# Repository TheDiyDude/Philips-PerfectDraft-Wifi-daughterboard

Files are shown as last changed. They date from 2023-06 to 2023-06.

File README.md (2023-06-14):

# Wifi Extension Board for Philips Perfect Draft (not Pro)
```
Ther are a couple of older approaches with potentiometers and switches to set a desired beer temperature.
Standard configuration is 3°C and sometimes this is to cold. Or you want to save energy. Which is not possible.
Here you can build your own PCB or other board type to add Wifi capabilities to your Perfect Draft machine (not Pro).

NOTE: Please pay additional attention if you work with high-voltage electricial power. If you are not aware of security when working with electricial power dont do this project. I am not responsible if you hurt youself or others. Your household AC current is between 110 and 240 volts and can kill you. Wiring errors lead into fire or turn your project into a leathal weapon!This is a diy project and you have to know what you are doing and think before you do something. Ok, I am a notorious german and we love these safety instructions. 
```

```
Features: 
  Wifi enabled
  Wifi Setup AP Mode (Wifi credentials stored in EEPROM)
  OTA Updates
  Set Cooling Temperature via Webbrowser http://PerfectDraft.local or IP
  Bypass your settings and use orginal NTC value (to see correct Temp after 5 Minutes)
  Use Fast Temp Buttons: 7°C, 10°, 11° C
  Save your setting within EEPROM and set after every reboot automatically
```
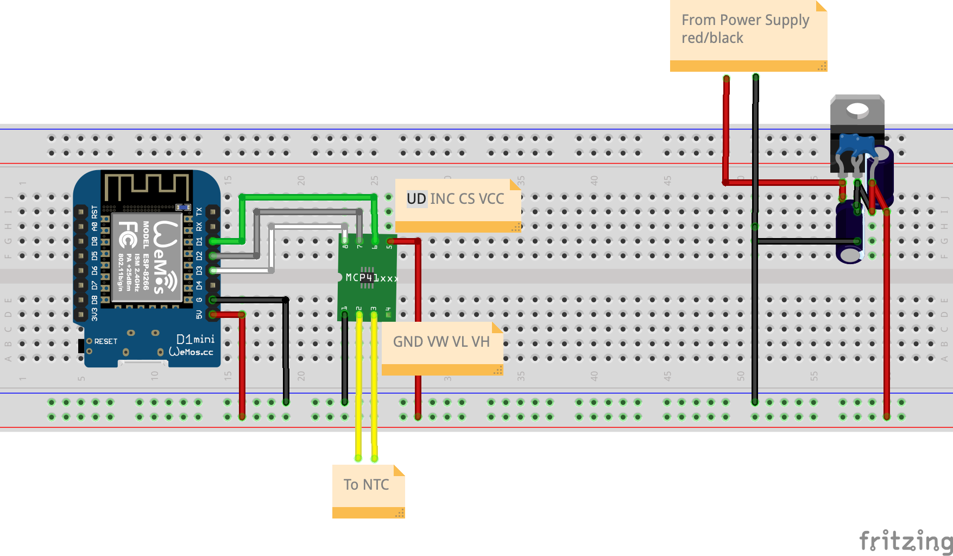
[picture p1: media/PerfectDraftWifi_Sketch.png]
Fritzing Sketch


```
Use a digital potentiometer like X9C103S (10kOhm) and connect the Pins:
VCC to 5V Pin 1
GND to 5V Pin 2
CS  to D1 Mini Pin D1
INC to D1 Mini Pin D2
U/D to D1 Mini Pin D3
VL  to one of the wires from the NTC connector (PD PCB)
VW  to the wire you have choose before (see description below)
```
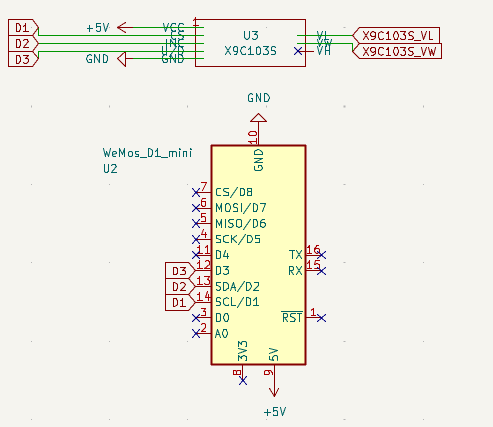
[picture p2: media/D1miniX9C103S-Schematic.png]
WemosD1-Wiring

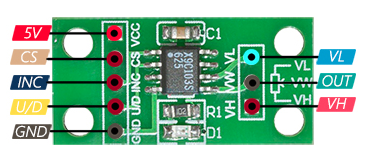
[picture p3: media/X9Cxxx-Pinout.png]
X9C103S


```
Remove the connector from PD PCB and add a Y connector. 
Choose one Pin from the PD PCB male connector labeled NTC and connect that wire to VL (X9C103S). 
The VW wire connect to the female connector (original) that was connected to the PD PCB before. 
The other Pin from the PCB labeled NTC connect directly to the female connector (original). 
```
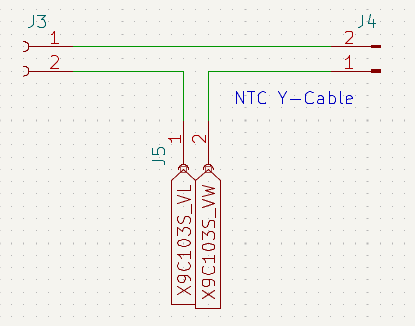
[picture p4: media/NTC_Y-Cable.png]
X9C103S_Y-Cable

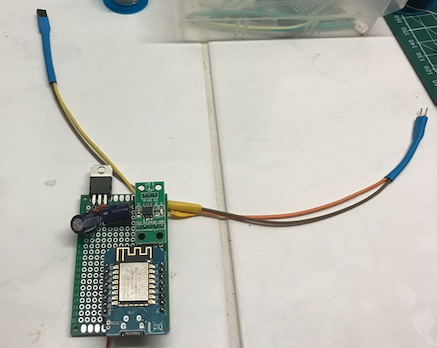
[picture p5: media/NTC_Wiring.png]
NTC Wiring


```
It is possible to use the machines power supply as it is already DC and 10.6V - 
apply this standard stabilized power converter to get 5V DC from 10.6 V DC:

Input  Pin 1 to PD red wire
Input  Pin 2 to PD black wire
Output Pin 1 to D1 Mini Pin 5V
Output Pin 2 to D1 Mini Pin get

See the second picture below to build a power supply Y-connector. Use the same cable connectors and connect red to PCB and to LM7805 Input Pin 1 - same to the black wire but connect that to Input Pin 2 (GND).
```
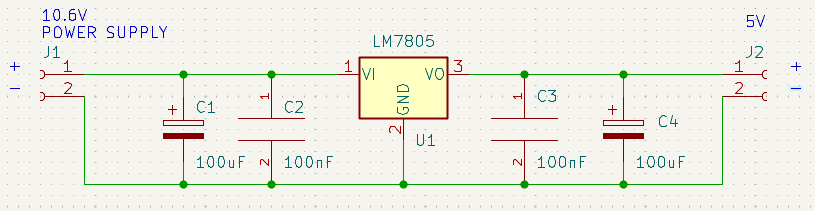
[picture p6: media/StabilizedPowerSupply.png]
stabilized power converter

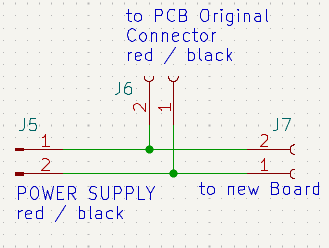
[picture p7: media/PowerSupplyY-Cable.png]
PowerSupplyY-Connector2

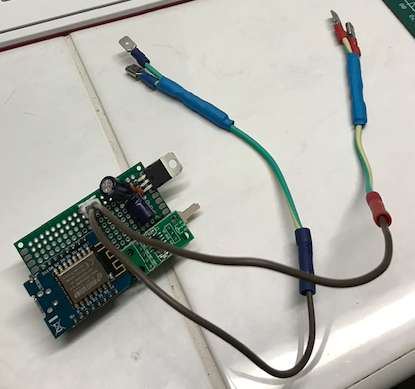
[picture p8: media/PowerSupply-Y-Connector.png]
PowerSupplyY-Connector

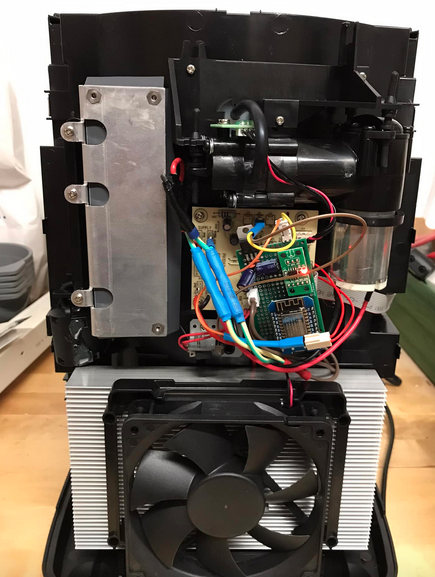
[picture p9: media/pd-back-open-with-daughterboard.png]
added-daughterboard

```
For communication with the X9C103S digital potentiometer I use the following supporting library:
   https://github.com/lucyamy/LapX9C10X.git
I do not know if this lib will change and I have put latest working copy to Libs folder. 
Add this ZIP library to your project.

Ensure to change your SSID and credentials before uploading the firmware. See firmware/Credentials.h
Ensure to change the default OTA credentials before uploading - default OTA upload password is 'pd2023'
Build the firmware and if you have done the wiring correctly you can see the Perfect Draft Wifi Website:
```
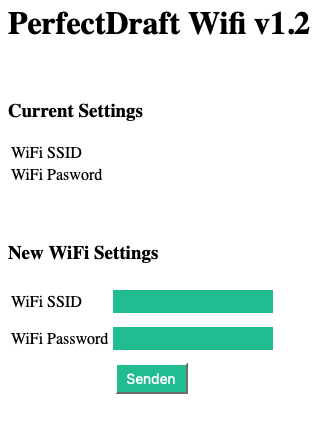
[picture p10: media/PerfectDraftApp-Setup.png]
<p style="text-align:center;">
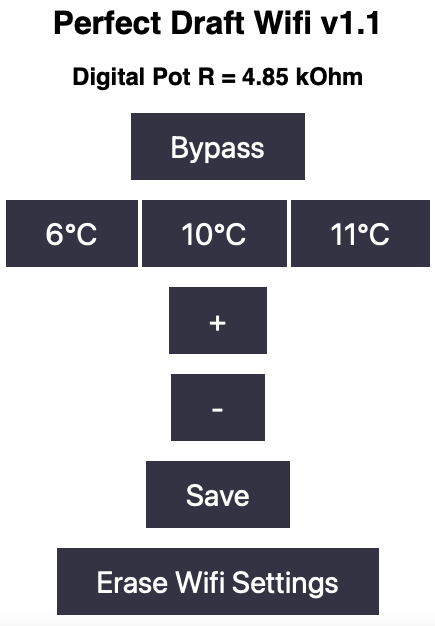
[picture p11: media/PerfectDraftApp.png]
</p>

After compiling and uploading you should be able to connect to your hostname (see Credentials.h for setting hostname):
```
22:10:06.872 -> Ready
22:10:10.113 -> IP address: 358.11.122.42
22:10:10.113 -> Setup completed
22:10:49.272 -> Client available
22:10:49.272 -> GET / HTTP/1.1
22:10:49.272 -> Host: perfectdraft-neu.local
22:10:49.272 -> Upgrade-Insecure-Requests: 1
22:10:49.272 -> Accept: text/html,application/xhtml+xml,application/xml;q=0.9,*/*;q=0.8
22:10:49.272 -> User-Agent: Mozilla/5.0 (Macintosh; Intel Mac OS X 10_15_6) AppleWebKit/605.1.15 (KHTML, like Gecko) Version/14.0.2 Safari/605.1.15
22:10:49.272 -> Accept-Language: de-de
22:10:49.272 -> Accept-Encoding: gzip, deflate
22:10:49.305 -> Connection: keep-alive
22:10:49.305 -> 
22:10:49.305 -> Client disconnected
22:10:49.305 -> 
```

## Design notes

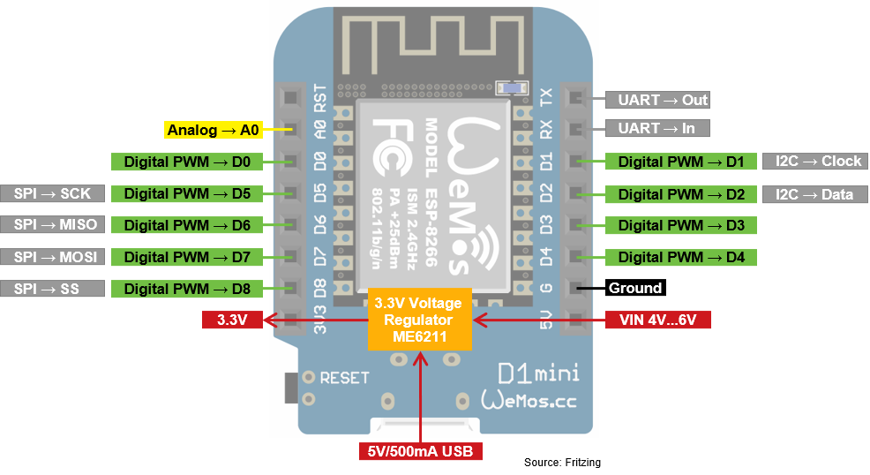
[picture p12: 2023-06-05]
media/ESP8266-WeMos-D1-Mini-Pinout.png

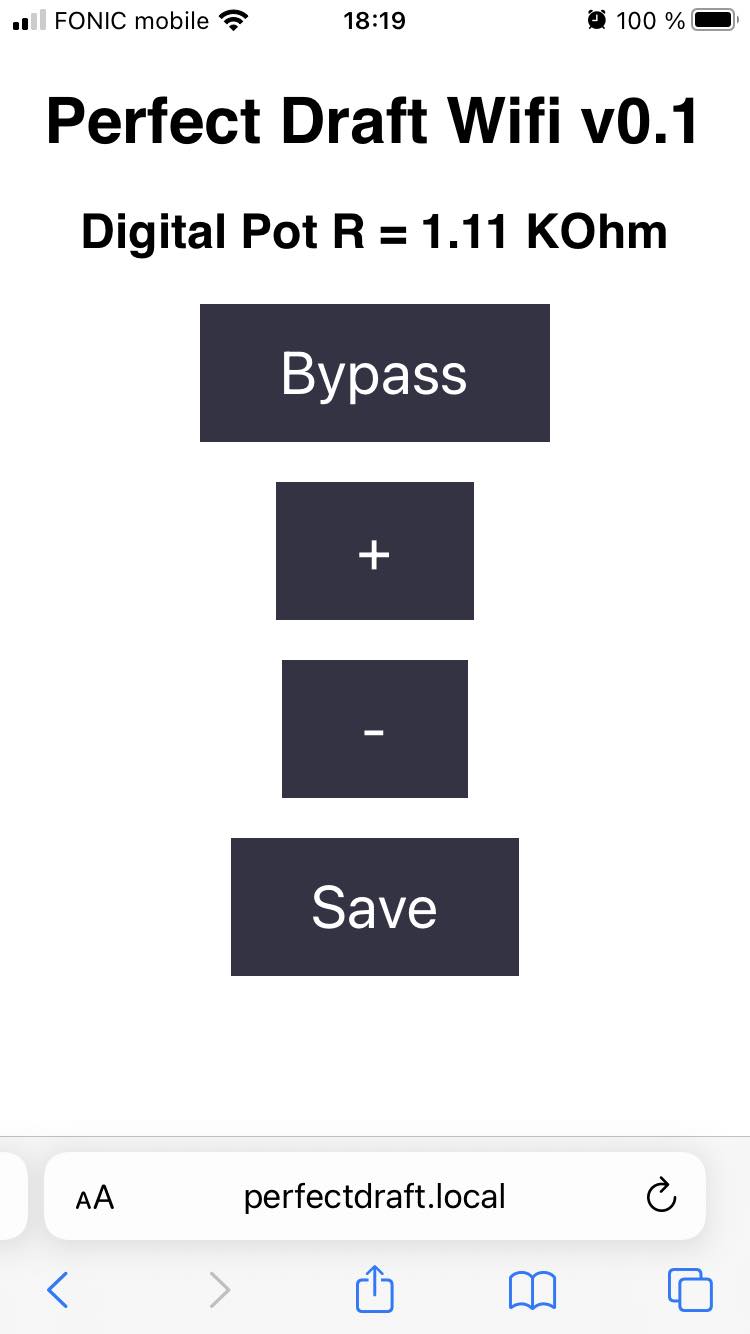
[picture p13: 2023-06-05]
media/C.jpg

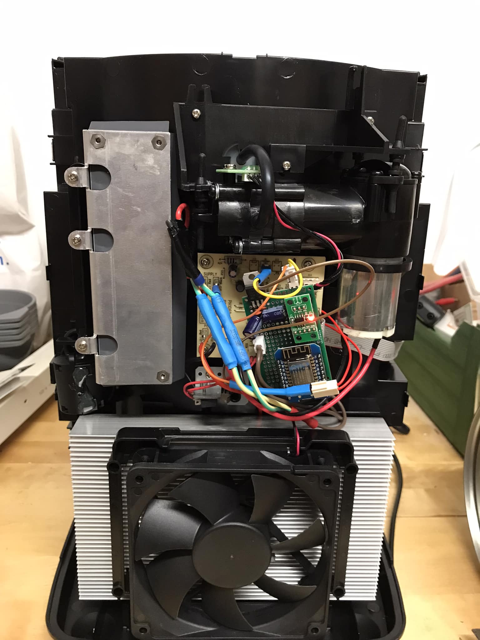
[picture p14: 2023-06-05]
media/B.jpg

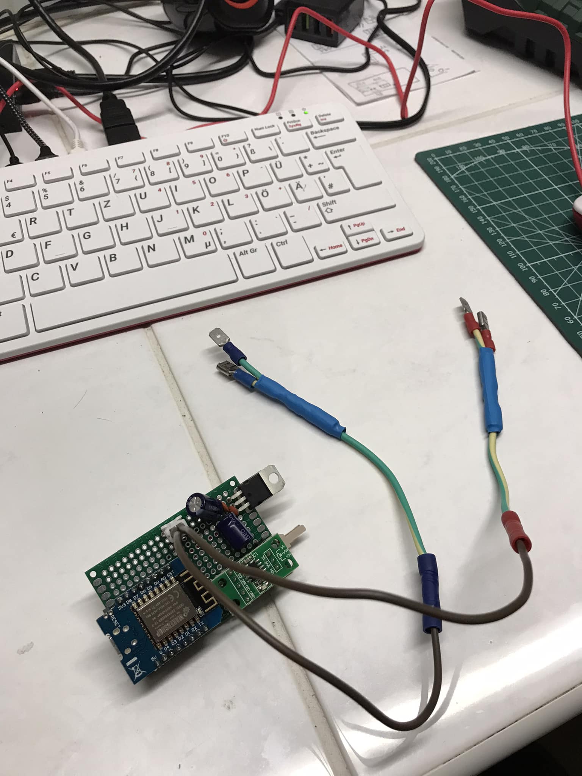
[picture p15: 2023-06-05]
media/A.jpg

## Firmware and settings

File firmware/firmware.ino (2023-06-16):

// Philips-PerfectDraft-Wifi-daughterboard
// Firmware to add Wifi  
// to your Perfect Draft Beer dispenser 
// and set cooling temperaure to a desired
// value, i.e 6°C, 7°C .. 
//
// Author: Marc-Oliver Blumenauer 
//         marc@l3c.de
//
// License: MIT
//  
//
#include <ESP8266WiFi.h>
#include <ESP8266WebServer.h>
#include <ESP8266HTTPClient.h>
#include <ESP8266mDNS.h>
#include <ArduinoOTA.h>
#include <LapX9C10X.h>
#include <EEPROM.h>

#include "Credentials.h"

// MQTT
#if defined(__MQTT_ENABLED__)
  #include <PubSubClient.h>
  WiFiClient espClient;
  PubSubClient mqtt(espClient);
  bool useMQTT = true;
  int mqttRetryCount = 0;
#endif

// X9C103 pins
#define CSPIN  D1
#define INCPIN D2
#define UDPIN  D3

LapX9C10X digPot(INCPIN, UDPIN, CSPIN, LAPX9C10X_X9C103);

// Port of our Web Server 
ESP8266WebServer server(80);

// For HTTP Request
char buffer[255];
String ssid, pass, content;
bool apmode = false;                              
String redirect = "<!DOCTYPE html><html><head><meta http-equiv=\"refresh\" content=\"0; url='/'\" /></head><body></body></html>";
float beerTemp = 0.0;

#if defined(__MQTT_ENABLED__)
char kOhm[30];
#endif

void setup() {
  Serial.begin(115200);
  Serial.println("Booting");
  readData();                                     //Check EEPROM for stored credentials
  if (ssid.length() == 0) {                       //If not found set AP mode
    ap_mode();
  } else {
    if (testWifi()) {                             //If found try to connect to WiFi AP
      Serial.println("WiFi Connected!!!");
      apmode = false;
      // Port defaults to 8266
      // ArduinoOTA.setPort(8266);
      ArduinoOTA.setHostname(ota_hostname);
      ArduinoOTA.setPassword(ota_password);
      ArduinoOTA.onStart([]() {
        Serial.println("Start");
      });
      ArduinoOTA.onEnd([]() {
        Serial.println("\nEnd");
      });
      ArduinoOTA.onProgress([](unsigned int progress, unsigned int total) {
        Serial.printf("Progress: %u%%\r", (progress / (total / 100)));
      });
      ArduinoOTA.onError([](ota_error_t error) {
        Serial.printf("Error[%u]: ", error);
        if (error == OTA_AUTH_ERROR) Serial.println("Auth Failed");
        else if (error == OTA_BEGIN_ERROR) Serial.println("Begin Failed");
        else if (error == OTA_CONNECT_ERROR) Serial.println("Connect Failed");
        else if (error == OTA_RECEIVE_ERROR) Serial.println("Receive Failed");
        else if (error == OTA_END_ERROR) Serial.println("End Failed");
      });
      ArduinoOTA.begin();
      EEPROM_Read(&beerTemp);
      if (beerTemp > 0.01 && beerTemp < 12.00) {
          digPot.set(beerTemp);
      } else {
          digPot.begin();
      }
      delay(5000);
      // MQTT 
      // initialize mqtt client
      #if defined(__MQTT_ENABLED__)
      Serial.print("connecting to MQTT host ");
      mqtt.setServer(mqtt_hostname, MQTT_PORT);
      mqtt.setCallback(callback);
      mqttRetryCount=0;
      if (!mqtt.connected()) {
            while (!mqtt.connected() && useMQTT) {
                mqtt.connect(ota_hostname,mqtt_username,mqtt_password);
                Serial.print(".");
                mqttRetryCount++;
                delay(1000);
                if (mqttRetryCount>=10) { useMQTT=false; }
            }
      }
      if (useMQTT) {
        Serial.println(". connected!");
        pub("status", "alive");
        sprintf(buffer,"/PerfectDraft/%s/setTemp",ota_hostname);
        mqtt.subscribe(buffer);
      }
      if (!useMQTT && mqttRetryCount>=10) {
        Serial.println(". failed!");
      }
      #endif  
      launchWeb(1);   
    } else {                                       
      ap_mode();
    }
  }
  Serial.println("Setup completed");
}

void loop() {
  ArduinoOTA.handle();
  #if defined(__MQTT_ENABLED__)
    mqtt.loop(); 
  #endif
  if (apmode) {
    server.handleClient();                        
  } else {
    if (WiFi.status() == WL_CONNECTED) {          
      server.handleClient();
      #if defined(__MQTT_ENABLED__)
        mqtt.loop(); 
      #endif
    }
  }
}
#if defined(__MQTT_ENABLED__)
void pub(const char* topic, const char* value) {
  if (mqtt.connected() && useMQTT) {
    sprintf(buffer,"/PerfectDraft/%s/%s",ota_hostname,topic);
    mqtt.publish(buffer,value);
    Serial.println("Sending to MQTT Broker:");
    Serial.println(buffer);
    Serial.println(value);
  }
}
void callback(char* topic, byte* payload, unsigned int length) {
  payload[length] = '\0';
  String s = String((char*)payload);
  int setTemp = s.toFloat();

  sprintf(buffer,"Message arrived [%s] %s",topic,s);
  Serial.println(buffer);

  if (setTemp >= 3 && setTemp <= 12) {
    Serial.println("setTemp in range!");
    switch(setTemp) {
      case  6: Serial.println("setTemp is 6 °C / Setting now 4.85 kOhm");
               digPot.set((float)4.8);
               break;
      case 10: Serial.println("setTemp is 10 °C / Setting now 5.66 kOhm");
               digPot.set((float)5.66);
               break;
      case 11: Serial.println("setTemp is 11 °C / Setting now 6.8 kOhm");
               digPot.set((float)6.8);
               break;                            
      default: sprintf(buffer,"This temperature currently not supported: %d °C",setTemp);
               Serial.println(buffer);
               break;      
    }
  }
}
#endif

void ap_mode() {                                  
  Serial.println("AP Mode. Please connect to http://192.168.4.1 to configure");
  apmode = true;
  const char* ssidap = "PerfectDraft-Setup";
  const char* passap = "";
  WiFi.mode(WIFI_AP);
  WiFi.softAP(ssidap, passap);
  Serial.println(WiFi.softAPIP());
  apmode = true;
  launchWeb(0);                                   
}

void launchWeb(int webtype) {
  createWebServer(webtype);
  server.begin();
}

void createWebServer(int webtype) {             
  if (webtype == 0) { 
    server.on("/", []() {
      content = "<html><head><style>.button {background-color: #3CBC8D;";
      content += "color: white;padding: 5px 10px;text-align: center;text-decoration: none;";
      content += "display: inline-block;font-size: 14px;margin: 4px 2px;cursor: pointer;}";
      content += "input[type=text],[type=password]{width: 100%;padding: 5px 10px;";
      content += "margin: 5px 0;box-sizing: border-box;border: none;";
      content += "background-color: #3CBC8D;color: white;}</style></head><body>";
      content += "<h1>PerfectDraft Wifi v1.2</h1><br>";
      content += "<h3>Current Settings</h3>";
      content += "<table><tr><td><label> WiFi SSID</label></td><td><label>" + ssid + "</label></td></tr>";
      content += "<tr><td><label> WiFi Pasword</label></td><td><label>" + pass + "</label></td></tr></table><br><br>";
      content += "<form method='get' action='setting'>";
      content += "<h3>New WiFi Settings</h3>";
      content += "<table><tr><td><label>WiFi SSID</label></td><td><input type='text' name = 'ssid' lenght=32 ></td></tr>";
      content += "<tr><td><label> WiFi Password</label></td><td><input type='password' name = 'password' lenght=32></td></tr>";
      content += "<tr><td></td><td><input class=button type='submit'></td></tr></table></form>";
      content += "</body></html>";
      server.send(200, "text/html", content);
    });
    server.on("/setting", []() {                  
      String ssidw = server.arg("ssid");
      String passw = server.arg("password");
      writeData(ssidw, passw);                    
      content = "Success..please reboot";
      server.send(200, "text/html", content);
      delay(2000);
      ESP.restart();
    });
    server.on("/clear", []() {                      
      clearData();
      delay(2000);
      ESP.restart();
    });
  }
  if (webtype == 1) {   
    server.on("/", []() {
      content  = "<!DOCTYPE html><html>";
      content += "<head><meta name=\"viewport\" content=\"width=device-width, initial-scale=1\">";
      content += "<link rel=\"icon\" href=\"data:,\">";
      content += "<style>html { font-family: Helvetica; display: inline-block; margin: 0px auto; text-align: center;}";
      content += ".button { background-color: #333344; border: none; color: white; padding: 16px 40px;";
      content += "text-decoration: none; font-size: 30px; margin: 2px; cursor: pointer;}";
      content += ".button2 {background-color: #888899;}</style></head>";
      content += "<body><h1 align=\"center\">Perfect Draft Wifi v1.2</h1>";
      sprintf(buffer,"<p><h2 align=\"center\">Digital Pot R = %4.2f kOhm</h2></p>",digPot.getK());
      content += buffer;
      content += "<p><a href=\"/Temp/bypass\"><button class=\"button\">Bypass</button></a></p>";
      content += "<p><a href=\"/Temp/6deg\"><button class=\"button\">6&deg;C</button></a>";
      content += "<a href=\"/Temp/10deg\"><button class=\"button\">10&deg;C</button></a>";
      content += "<a href=\"/Temp/11deg\"><button class=\"button\">11&deg;C</button></a></p>";
      content += "<p><a href=\"/Temp/inc\"><button class=\"button\">+</button></a></p>";
      content += "<p><a href=\"/Temp/dec\"><button class=\"button\">-</button></a></p>";
      content += "<p><a href=\"/Temp/store\"><button class=\"button\">Save</button></a></p>";
      content += "<p><a href=\"/clear\"><button class=\"button\">Erase Wifi Settings</button></a></p>";
      content += "</body></html>";
      server.send(200, "text/html", content);
    });
    server.on("/clear", []() {                      
      clearData();
      delay(2000);
      ESP.restart();
    });
    server.on("/Temp/inc", []() {
      Serial.println("Temp: Incrementing");
      digPot.offset(+1);
      #if defined(__MQTT_ENABLED__)
        sprintf(kOhm,"%4.2f",digPot.getK());
        pub("kOhm",kOhm);
      #endif
      delay(100);
      server.send(200, "text/html", redirect);
    }); 
    server.on("/Temp/dec", []() {
      Serial.println("Temp: Decrementing");
      digPot.offset(-1);
      #if defined(__MQTT_ENABLED__)
        sprintf(kOhm,"%4.2f",digPot.getK());
        pub("kOhm",kOhm);
      #endif
      delay(100);
      server.send(200, "text/html", redirect);
    });
    server.on("/Temp/bypass", []() {
      Serial.println("Temp: Bypass digital potentiometer");
      digPot.set(0);
      #if defined(__MQTT_ENABLED__)
        pub("BeerTemp","3");
        sprintf(kOhm,"%4.2f",digPot.getK());
        pub("kOhm",kOhm);
      #endif
      delay(100);
      server.send(200, "text/html", redirect);
    });
    server.on("/Temp/store", []() {
      Serial.println("Temp: store current value in NVRAM");
      digPot.writeNVM();
      delay(100);
      beerTemp = digPot.getK();
      EEPROM_Write(&beerTemp);
      server.send(200, "text/html", redirect);
    }); 
    server.on("/Temp/6deg", []() {
      Serial.println("Temp: set to 6°C ");
      digPot.set((float)4.8);
      #if defined(__MQTT_ENABLED__)
        pub("BeerTemp","6");
        sprintf(kOhm,"%4.2f",digPot.getK());
        pub("kOhm",kOhm);
      #endif
      delay(100);
      server.send(200, "text/html", redirect);
    });
    server.on("/Temp/10deg", []() {
      Serial.println("Temp: set to 10°C ");
      digPot.set((float)5.66);
      #if defined(__MQTT_ENABLED__)
        pub("BeerTemp","10");
        sprintf(kOhm,"%4.2f",digPot.getK());
        pub("kOhm",kOhm);
      #endif
      delay(100);
      server.send(200, "text/html", redirect);
    });
    server.on("/Temp/11deg", []() {
      Serial.println("Temp: set to 11°C ");
      digPot.set((float)6.8);
      #if defined(__MQTT_ENABLED__)
        pub("BeerTemp","11");
        sprintf(kOhm,"%4.2f",digPot.getK());
        pub("kOhm",kOhm);
      #endif
      delay(100);
      server.send(200, "text/html", redirect);
    });
  }
}
void EEPROM_Write(float *num)
{
  EEPROM.begin(512);
  byte ByteArray[4];
  int memPos = 100;
  memcpy(ByteArray, num, 4);
  for(int x = 0; x < 4; x++) { EEPROM.write((memPos++ + 4) + x, ByteArray[x]); }  
  EEPROM.end();
  Serial.print("Stored EEPROM Beer Temp: ");
  Serial.println(*num,2);
}
void EEPROM_Read(float *num)
{
  EEPROM.begin(512);
  byte ByteArray[4];
  int memPos = 100;
  for(int x = 0; x < 4; x++) { ByteArray[x] = EEPROM.read((memPos++ + 4) + x); }
  memcpy(num, ByteArray, 4);
  EEPROM.end();
  Serial.print("Read EEPROM Beer Temp: ");
  Serial.println(*num,2);
}
void readData() {                                 
  EEPROM.begin(512);
  Serial.println("Reading From EEPROM..");
  for (int i = 0; i < 50; i++) {                  
    if (char(EEPROM.read(i)) > 0) {
      ssid += char(EEPROM.read(i));
    }
  }
  for (int i = 50; i < 100; i++) {                 
    if (char(EEPROM.read(i)) > 0) {
      pass += char(EEPROM.read(i));
    }
  }
  Serial.println("Wifi ssid: " + ssid);
  Serial.println("Wifi password: " + pass);
  EEPROM.end();
}
void writeData(String a, String b) {              
  clearData();                                    
  EEPROM.begin(512);                              
  Serial.println("Writing to EEPROM...");
  for (int i = 0; i < 50; i++) {                  
    EEPROM.write(i, a[i]);
  }
  for (int i = 50; i < 100; i++) {                 
    EEPROM.write(i, b[i - 50]);
    Serial.println(b[i]);
  }
  EEPROM.commit();
  EEPROM.end();
  Serial.println("Write Successfull");
}
void clearData() {                                
  EEPROM.begin(512);
  Serial.println("Clearing EEPROM ");
  for (int i = 0; i < 512; i++) {
    Serial.print(".");
    EEPROM.write(i, 0);
  }
  EEPROM.commit();
  EEPROM.end();
}
boolean testWifi() {                            
  WiFi.softAPdisconnect();
  WiFi.disconnect();
  WiFi.mode(WIFI_STA);
  WiFi.begin(ssid.c_str(), pass.c_str());
  int c = 0;
  while (c < 30) {
    if (WiFi.status() == WL_CONNECTED) {
      WiFi.setAutoReconnect(true);
      WiFi.persistent(true);
      Serial.println(WiFi.status());
      Serial.println(WiFi.localIP());
      delay(100);
      return true;
    }
    Serial.print(".");
    delay(900);
    c++;
  }
  Serial.println("Connection time out...");
  return false;
}
